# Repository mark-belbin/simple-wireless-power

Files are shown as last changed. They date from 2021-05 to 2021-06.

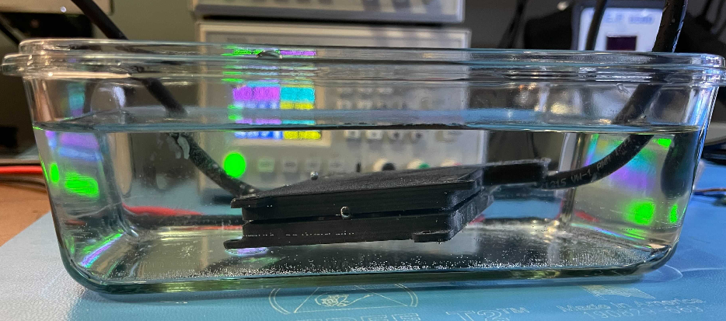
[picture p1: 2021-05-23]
docs/images/Water Setup.PNG

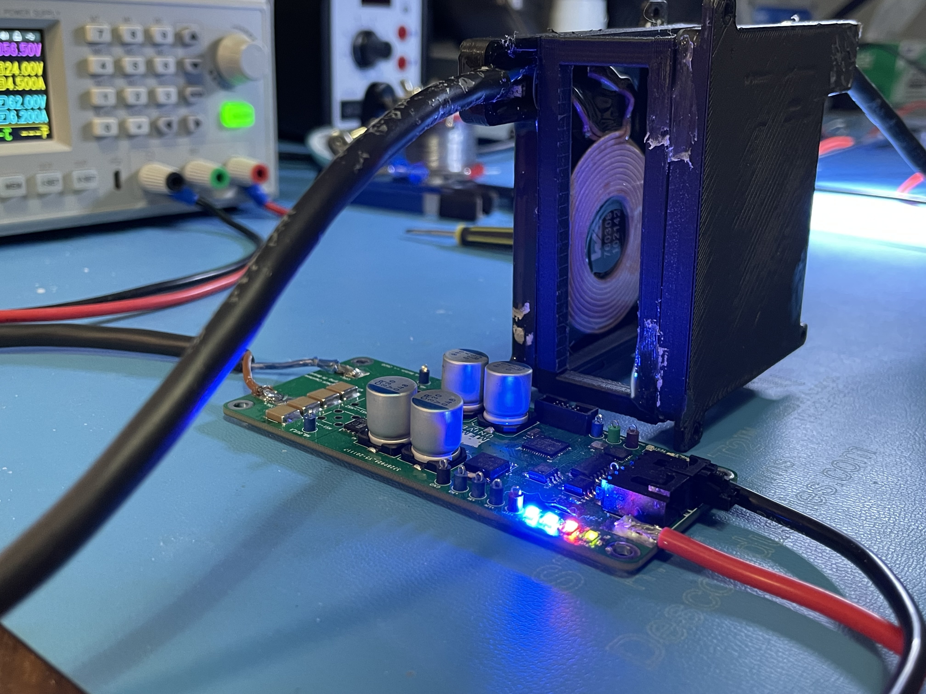
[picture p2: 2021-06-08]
docs/images/Gap Test.jpg

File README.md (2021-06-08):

# Simple Wireless Power System

## Introduction 
This project is a simple two-board wireless power system that can transmit up to 100W at close distances. Originally it was designed as a small part of a subsea resident autonomous underwater vehicle senior design project. The goal was to have a contactless method to charge the vehicles battery in an underwater docking station, versus a contact method like a wetmate connector. This reduces the chance for failure in a harsh ocean environment. Included in this repository are schematics, PCB design files, LTspice simulations, and embedded code.

TX Board Powered

## Design Topology
At the start of my wireless power investigation, it was initially decided to create a type of "coreless transformer" to keep things simple. This type of design would transfer power by simply placing two identical coils as close as possible to each other. The closer the coils, the higher their mutal inductance and coupling coefficient. The coupling coefficient directly equals the maximum achievable efficiency; k=0.7 would mean 70% efficiency for example. 

coreless_transformer
> Coreless transformer equivalent circuit.

However, since a lot of work was already being placed into research and simulation anyways, it was decided to try and create a resonant system. Using capactiors, resonant circuits can be created with the inductive transmitter and reciever coils, increasing efficiency accross the wireless link. This is the de facto inductive wireless power transfer method used in industry, and it turned out to be simpler than thought. The topology chosen is called "series-series" resonant inductive wireless power transfer, which means that the compensating capacitors are placed in series with both the transmit and recieve coils. Other topologys exist such as "series-parallel" or "parallel-parallel" which place the capacitors in parallel with the coils as well.

series_series
> Series-series topology circuit.

## Hardware
The system consists of a transmitter (TX) PCB and a reciever (RX) PCB. Both are 4 layer 1oz copper boards that are 100x45mm. The designs were completed using KiCAD EDA (http://kicad-pcb.org/), a free and open source PCB design software that is highly recommended. 

### TX Board
The transmitter board's primary purpose is to take a DC input voltage and pass it through a full bridge inverter to create a high frequency sinusoidal voltage. This sinusoidal voltage passes through the compensating capacitors and transmitter coil, and creates an alternating magnetic field that couples to the reciever coil. The H-Bridge is designed around an operating point of 24VDC input, 100kHz switching frequency, and up to 100W of transfer power. The main limiter for power transfer is the rated voltage and current of the coils and compensating capacitors. The MOSFETs of the H-Bridge are over-speced to minimize losses. Short circuit protection circuitry is included on the TX board, since if the TX coil is open-loaded during operation it will appear as a short to the input power supply.

TX Board

The TX board also has an embedded SAMD21 microntroller which generates the nessecary PWM signal for the gate drivers. Further, the board includes a CAN controller and transceiver so that it could potentially be commanded on/off and relay power transfer telemetry to a remote control computer via CANBus.

TX Schematic

### RX Board
The RX board is much simpler than the TX board. It has no microcontroller, and uses passive schottky diodes in a full bridge rectifier configuration to convert the recieved AC voltage back to a usable DC voltage. An simple overvoltage protection scheme is incorporated in the RX board to prevent an overvoltage event downstream. A schmitt trigger circuit watches the output voltage, and if it is too high, connects the output to a bank of bleeder resistors. The extra load on the output subsequently draws down the voltage before it reaches a harmful level. 
                                                                                   
RX Board

RX Schematic

### Key Components

#### Coils
The transmitter and reciever coils are identical. They were sourced on Digi-Key from Wurth Electronics, PN 732-9670-ND. They have an inductance of 5.8uH, and a very low series resistance, allowing for high current rating. I think these are probably the highest current rated coils you can find on Digikey when I selected them! As well, Wurth was kind enough to provide ample documentation for the coils. A key piece of data was a graph of their Quality factor (Q) versus frequency. The higher the quality factor, the better the efficiency. Therefore, since the Q peaked at around 100-101kHz, that was the selected operating frequency for the entire system.

Coils
> Coils encased and epoxyed in a custom mount for underwater use in the original AUV application. 

#### Series Capacitors
Four 100nF capacitors were placed in parallel to achieve the desired ~380-400nF series capacitance. Large 2220 package ceramic capacitors were chosen for their desirable low series resistance. The final parts were chosen from Murata Electronics and sourced on Digikey, PN 490-16696-1-ND. These capacitors were compared against others, again looking at their quality factor over frequency. The series capacitors ended up being the weakest link in the system, and would fail on the TX side when delivering over 5-6A. These caps had the best that could be found at the time, but if someone knows of a better or higher current-carrying choice, let me know! 

#### MOSFETs
The MOSFETs chosen are low-loss N-Channel devices. The final parts chosen are from Infineon and sourced on Digi-Key, PN 448-IAUC70N08S5N074ATMA1CT-ND. These FETs were selected for the lowest possible loss, taking into account both resistive and switching losses. 

#### Diodes
The diodes for the full-bridge rectifier were chosen again for as low of loss as possible. Really, the low voltage and high current environment is probably better suited for active rectification, but to keep things simple passive rectification was chosen. The best diodes for this are schottky due to their low forward voltage. The final parts chosen are from ON Semi and sourced from Digi-Key, PN FSV12100VCT-ND. A few different diode models were selected and simulated in the final circuit, and this model ended up producing the lowest loss. 

#### Micro Controller
The chosen microcontroller is the SAMD21G18A, PN ATSAMD21G18A-MF-ND. This is the same microcontroller that is on the Arduino Zero dev board, and our senior design team already knew how to easily program and flash it. Perhaps someone could modify this design and retrofit a more popular microcontroller, like an STM32.

## Software
The current software developed for this project is the embedded code on the TX board's SAMD21 microcontroller. Code was developed using the Arduino IDE for simplicity. A .bin file was generated and then uploaded to the microcontroller using a J-Link EDU programmer. The code is about as simple as it gets, just generating a 50% duty cycle, 100kHz PWM signal. No feedback is incorporated since it is assumed that there is no expected communication between TX and RX boards in the original underwater application. 

## Simulation
The entire end-to-end wireless power system was simulated in LTspice. The simulation aided in component selection, and gave an initial estimate of efficiency greater than 90%. It's hard to say how accurate the simulation is, since it's not clear what coupling factor, k, will be present in a real world system. Any tips on WPT system simulation in LTspice would be greatly appreciated! 

Sim Schematic

## Testing Results
The system was tested with surpising results. At a gap distance of about 1-2mm, as close as we could get, the system was able to transfer power up to 100W at an efficiency of 81.3%. Testing different frequencies between 95-105kHz did not show any noticeable difference in efficiency. The coils were also submerged in saltwater to check efficiency versus the in-air test. There was no measurable difference in water, salt or fresh.

Lab Test Setup

Water Setup

Another interesting outcome was shown in the thermal images during testing. The hottest components in the system were the series capacitors, reaching upwards of 70C degrees after 5 mins of operation. No heatsink or airflow meant that these are probably worst case numbers, but still perhaps the capacitors could be underspec'd for the application. At 100W delivered, about 20W is lost in the system, and the series capacitors are the only noticeable components that heat up significantly. It's a bit inconcievable that all the 20W is split amongst 8 small capacitors, so I assume that there are some losses in the surrounding air that are radiated away. It's hard to tell, would definitely be open to some insight on this if anyone has encountered this before! 

capacitor_thermals

Efficiency vs coil gap distance measurements were completed with some interesting results. First, efficiency seems to drop linearly from 0-20mm. This is cool since it seems that the resonant effect is indeed working. Normally a magnetic field would decrease with the distance squared, a non-linear relationship. As well, when reaching 20mm or beyond, the TX board was limited by its series current capability. More series current is required in to the transmitter coil to achieve the same power transfer as efficiency drops. The series capacitors on the TX board were the limiter, as they started to fail beyond 6A. A heatsink and forced air could give them a bit of extra capability potentially. I'd be interested in hearing about any better capacitor choices for higher series current while maintaining low loss accross them, or perhaps if a parallel-series or parallel-parallel topology would solve this problem.

Gap Test

GapGraph

## Discussion
This was a fun project and a small part of a much larger senior design project. 80-75% efficiency for 0-5mm coil gap satisfies the original design problem, which was to safely deliver 50W underwater at a 0-5mm gap distance. Always open for discussion or any tips on how this could have been done better. For a future project I'm interested in trying to make a super small low power version that could deliver 5-10W for underwater sensor applications.

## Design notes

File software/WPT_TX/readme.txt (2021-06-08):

Software:
Programming Notes
Install arduino zero boards
Arduino IDE, Export Binary,
program bin with segger j flash and jlink edu
But in boards.txt edit with to 'without' under arduino zero board

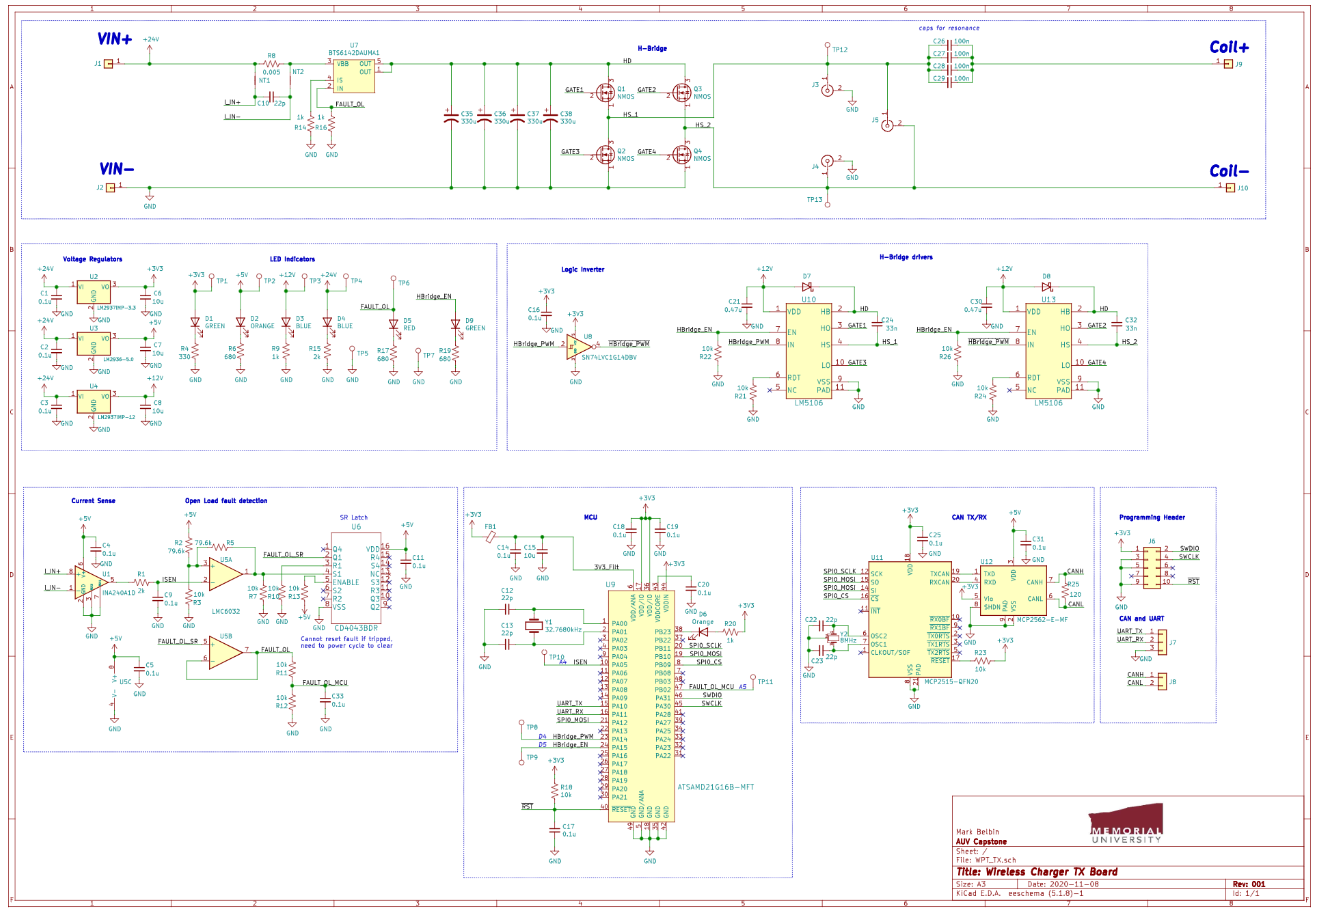
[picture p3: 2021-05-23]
docs/images/TX Schematic.PNG

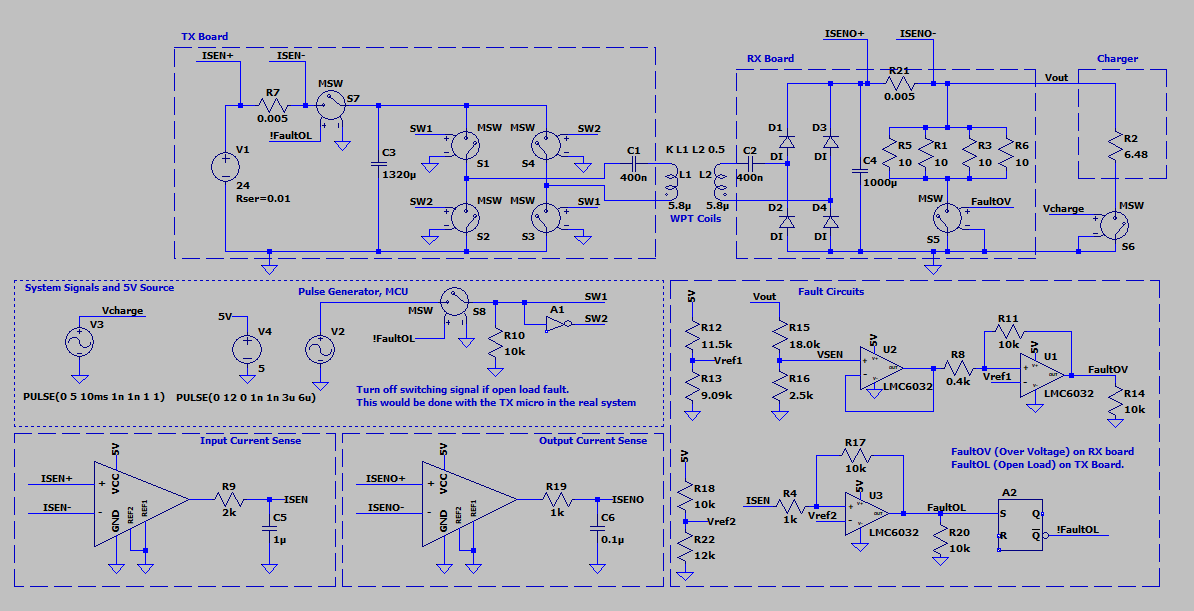
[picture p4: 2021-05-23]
docs/images/Sim Schematic.PNG

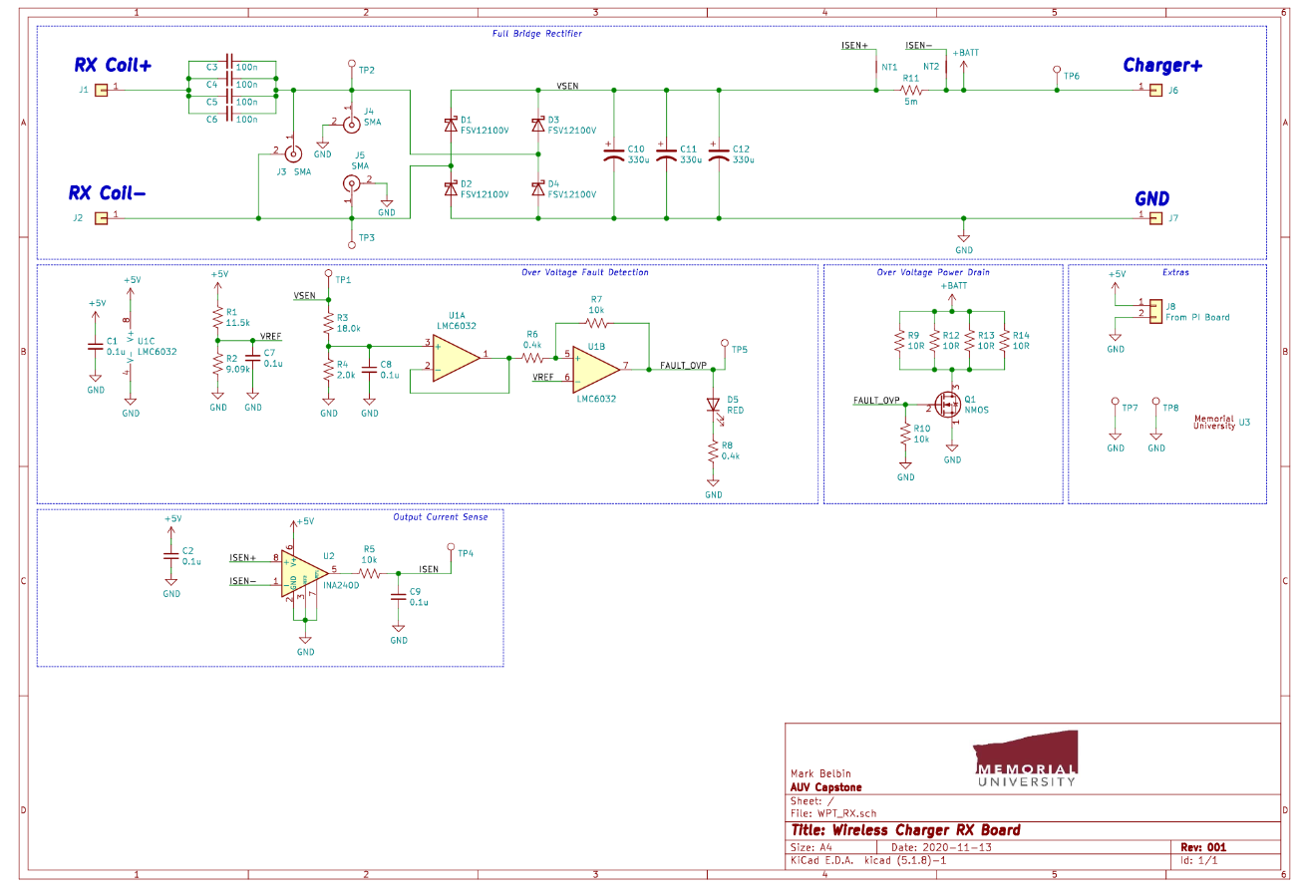
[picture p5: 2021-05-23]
docs/images/RX Schematic.PNG

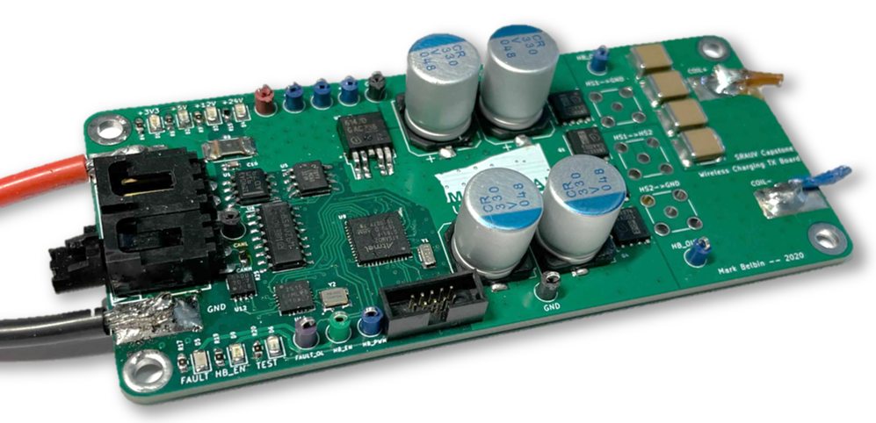
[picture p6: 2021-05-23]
docs/images/TX Board.PNG

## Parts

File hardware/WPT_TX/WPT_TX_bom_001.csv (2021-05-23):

Component | Description | Part | References | Value | Footprint | Quantity Per PCB | Datasheet | Digikey
1 | Unpolarized capacitor, small symbol | C_Small | C1 C2 C3 C4 C5 C9 C11 C14 C16 C17 C18 C19 C20 C25 C31 C33 | 0.1u | C_0603_1608Metric | 16 | ~ | 1276-1941-1-ND 1276-1258-1-ND
2 | Unpolarized capacitor, small symbol | C_Small | C21 C30 | 0.47u | C_0805 | 2 | ~ | 478-10438-1-ND
3 | Unpolarized capacitor, small symbol | C_Small | C26 C27 C28 C29 | 100n | C_2220 | 4 | ~ | 490-16696-1-ND
4 | Unpolarized capacitor, small symbol | C_Small | C15 | 10u | C_0603_1608Metric | 1 | ~ | 490-7201-1-ND
5 | Unpolarized capacitor, small symbol | C_Small | C6 C7 C8 | 10u | C_1206 | 3 | ~ | 1276-6767-1-ND
6 | Unpolarized capacitor, small symbol | C_Small | C10 C12 C13 C22 C23 | 22p | C_0603_1608Metric | 5 | ~ | 720-VJ0603A220JXBACCT-ND
7 | Unpolarized capacitor, small symbol | C_Small | C24 C32 | 33n | C_0805 | 2 | ~ | 445-172691-1-ND
8 | Light emitting diode | LED | D3 D4 | BLUE | LED_0805_2012Metric | 2 | ~ | 160-1579-1-ND
9 | Schottky diode | D_Schottky | D7 D8 | D_Schottky | D_SMA | 2 | ~ | SS16T3GOSCT-ND
10 | Light emitting diode | LED | D1 D9 | GREEN | LED_0805_2012Metric | 2 | ~ | 160-1423-1-ND
11 | Light emitting diode | LED | D2 D6 | ORANGE | LED_0805_2012Metric | 2 | ~ | 160-1413-1-ND
12 | Light emitting diode | LED | D5 | RED | LED_0805_2012Metric | 1 | ~ | 475-1415-1-ND
13 | Ferrite bead, small symbol | Ferrite_Bead_Small | FB1 | FB | L_0805_2012Metric | 1 | ~ | 490-9706-1-ND
14 | Generic connector, single row, 01x01, script generated (kicad-library-utils/schlib/autogen/connector/) | Conn_01x01 | J1 J2 J9 J10 | Conn_01x01 | SolderWirePad_single_SMD_5x10mm | 4 | ~
15 | Generic connector, single row, 01x03, script generated (kicad-library-utils/schlib/autogen/connector/) | Conn_01x03 | J7 | Conn_01x03 | 70553-03 | 1 | ~ | WM4154-ND
16 | Generic connector, single row, 01x02, script generated (kicad-library-utils/schlib/autogen/connector/) | Conn_01x02 | J8 | Conn_01x04 | 70553-02 | 1 | ~ | WM4900-ND
17 | Generic connector, double row, 02x05, odd/even pin numbering scheme (row 1 odd numbers, row 2 even numbers), script generated (kicad-library-utils/schlib/autogen/connector/) | Conn_02x05_Odd_Even | J6 | Conn_02x05_Odd_Even | Pin_Header_Straight_2x05_Pitch1.27mm | 1 | ~ | 1175-1627-ND
18 | coaxial connector (BNC, SMA, SMB, SMC, Cinch/RCA, ...) | Conn_Coaxial | J3 J4 J5 | Conn_Coaxial | SMA_Amphenol_901-144_Vertical | 3 | ~ | WM17068-ND
19 | Net tie, 2 pins | Net-Tie_2 | NT1 NT2 | Net-Tie_2 | NetTie-2_SMD_Pad0.25mm | 2 | ~
20 | N-MOSFET transistor, source/gate/drain | Q_NMOS_SGD | Q1 Q2 Q3 Q4 | NMOS | TDSON-8-1 | 4 | https://www.infineon.com/dgdl/Infineon-IAUC70N08S5N074-DS-v01_00-EN.pdf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 | 448-IAUC70N08S5N074ATMA1CT-ND
21 | Resistor, US symbol | R_US | R8 | 0.005 | R_2512_Sense | 1 | ~ | YAG6124CT-ND
22 | Resistor, US symbol | R_US | R3 R7 R10 R11 R12 R13 R18 R21 R22 R23 R24 R26 | 10k | R_0603_1608Metric | 12 | ~ | RHM10KDCT-ND
23 | Resistor, US symbol | R_US | R25 | 120 | R_0603_1608Metric | 1 | ~ | P120BYTR-ND
24 | Resistor, US symbol | R_US | R9 R14 R16 R20 | 1k | R_0603_1608Metric | 4 | ~ | RHM1.0KDCT-ND
25 | Resistor, US symbol | R_US | R1 R15 | 2k | R_0603_1608Metric | 2 | ~ | 541-2790-1-ND
26 | Resistor, US symbol | R_US | R4 | 330 | R_0603_1608Metric | 1 | ~ | RHM330DCT-ND
27 | Resistor, US symbol | R_US | R6 R17 R19 | 680 | R_0603_1608Metric | 3 | ~ | RHM680DCT-ND
28 | Resistor, US symbol | R_US | R2 R5 | 79.6k | R_0603_1608Metric | 2 | ~ | 13-RT0603BRD0779K6LCT-ND
29 | IC MCU 32BIT 64KB FLASH 48QFN | ATSAMD21G16B-MFT | U9 | ATSAMD21G16B-MFT | TQFP-48_7x7mm | 1 | http://www.microchip.com/mymicrochip/filehandler.aspx?ddocname=en590209 | ATSAMD21G18A-MF-ND
30 |  | BTS6142DAUMA1 | U7 | BTS6142DAUMA1 | TO-252-4 | 1 | https://www.infineon.com/dgdl/Infineon-BTS6142D-DS-v01_01-EN.pdf?fileId=5546d4625a888733015aa3da1e0e1026 | BTS6142DAUMA1CT-ND
31 |  | CD4043BDR | U6 | CD4043BDR | SOIC-16_3.9x9.9mm_Pitch1.27mm | 1 |  | 296-31496-1-ND
32 | High- and Low-Side, Bidirectional, Zero-Drift, Current-Sense Amplifier With Enhanced PWM Rejection, 20V/V, SOIC-8 | INA240A1D | U1 | INA240A1D | SOIC-8_3.9x4.9mm_P1.27mm | 1 | http://www.ti.com/lit/ds/symlink/ina240.pdf | 296-48837-ND
33 | 50mA Ultra-Low Quiescent Current LDO Voltage Regulator, 5.0V fixed output, TO-252/SOT-223 | LM2936-5.0 | U3 | LM2936-5.0 | SOT-223-3_TabPin2 | 1 | http://www.ti.com/lit/ds/symlink/lm2936.pdf | 296-37374-1-ND
34 | 500-mA Low Dropout Regulator, SOT-223 | LM2937xMP | U4 | LM2937IMP-12 | SOT-223-3_TabPin2 | 1 | http://www.ti.com/lit/ds/symlink/lm2937.pdf | LM2937IMP-12/NOPBCT-ND
35 | 500-mA Low Dropout Regulator, SOT-223 | LM2937xMP | U2 | LM2937IMP-3.3 | SOT-223-3_TabPin2 | 1 | http://www.ti.com/lit/ds/symlink/lm2937.pdf | LM2937IMPX-3.3/NOPBCT-ND
36 |  | LM5106SD_NOPB | U10 U13 | LM5106 | LM5106SD | 2 |  | LM5106SD/NOPBCT-ND
37 | Precision CMOS Dual Operational Amplifier, DIP-8/SOIC-8 | LMC6082 | U5 | LMC6032 | SOIC-8_3.9x4.9mm_Pitch1.27mm | 1 | http://www.ti.com/lit/ds/symlink/lmc6082.pdf | 296-49646-1-ND
38 |  | MCP2515-QFN20 | U11 | MCP2515-QFN20 | TSSOP-20_4.4x6.5mm_P0.65mm | 1 |  | MCP2515-E/ML-ND
39 | High-Speed CAN Transceiver, 1Mbps, 5V supply, Vio pin, -40C to +125C, DFN-8 | MCP2562-E-MF | U12 | MCP2562-E-MF | DFN-8-1EP_3x3mm_P0.65mm_EP1.55x2.4mm | 1 | http://ww1.microchip.com/downloads/en/DeviceDoc/25167A.pdf | MCP2562-E/MF-ND
40 | Single Schmitt-Trigger Inverter, SOT-23 | SN74LVC1G14DBV | U8 | SN74LVC1G14DBV | SOT-23-5 | 1 | http://www.ti.com/lit/ds/symlink/sn74lvc1g14.pdf | 296-35944-1-ND
41 | Two pin crystal | Crystal | Y1 | 32.7680kHz | Crystal_SMD_3215-2pin_3.2x1.5mm | 1 | ~ | 887-2605-1-ND
42 | Three pin crystal, GND on pin 2, small symbol | Crystal_GND2_Small | Y2 | 8MHz | OSCCC320X250 | 1 | ~ | 2151-RH100-8.000-20-3050-EXT-TRCT-ND
Component Groups: | 42
Component Count: | 100
Fitted Components: | 100
Number of PCBs: | 1
Total components: | 100
Schematic Version: | 001
Schematic Date: | 2020-11-08
PCB Variant: | [u'default']
BoM Date: | 2020-11-08 10:35:57 PM
Schematic Source: | D:\AUV Capstone\AUV-Senior-Design\Mark\WPT_TX\WPT_TX.sch
KiCad Version: | Eeschema (5.1.8)-1

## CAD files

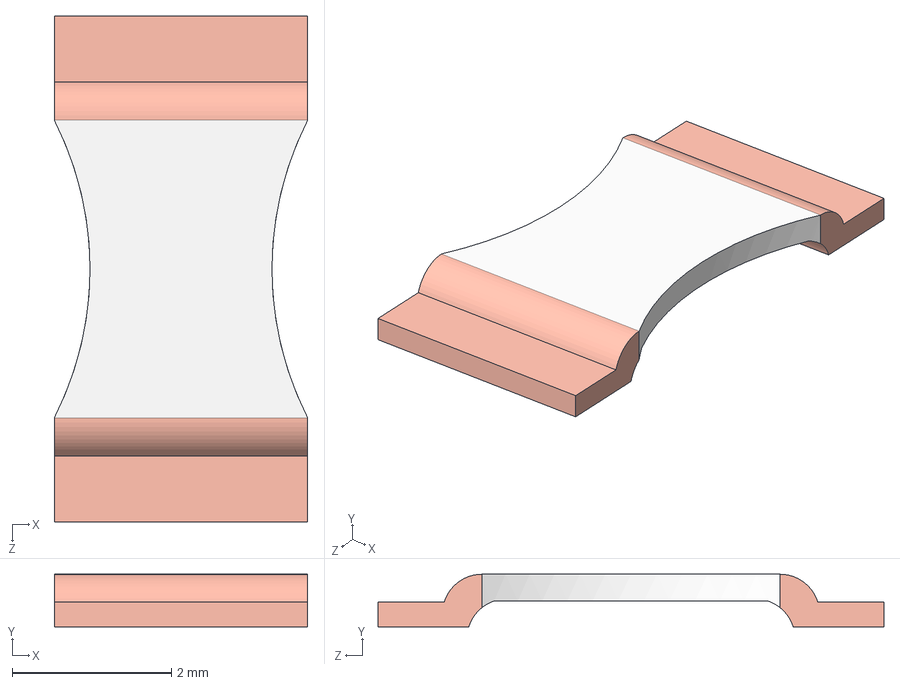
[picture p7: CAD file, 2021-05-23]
hardware/WPT_RX/3D Models/Sense Resistor.STEP
3.18 x 0.66 x 6.35 mm

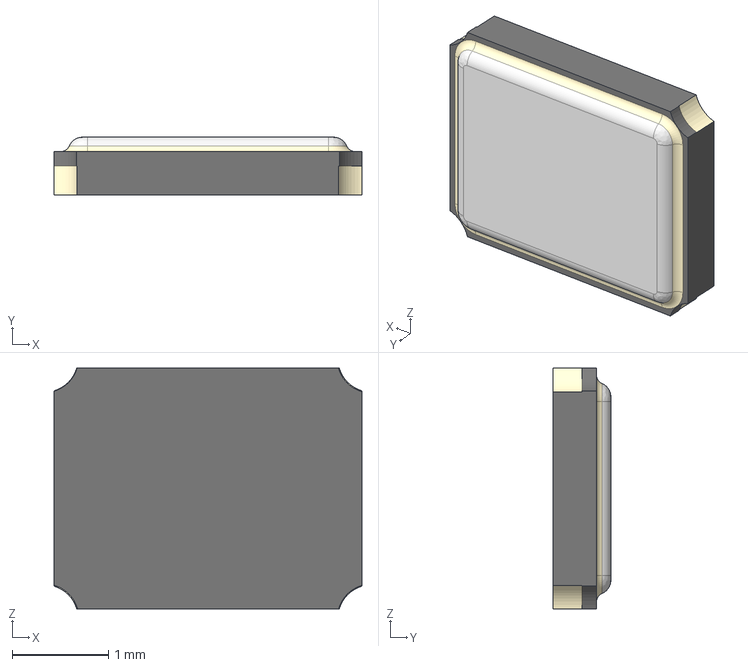
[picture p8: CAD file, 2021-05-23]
hardware/WPT_RX/3D Models/KX7 SMD Quartz Crystal Resonator 3.2x2.5mm.step
3.20 x 0.6 x 2.50 mm

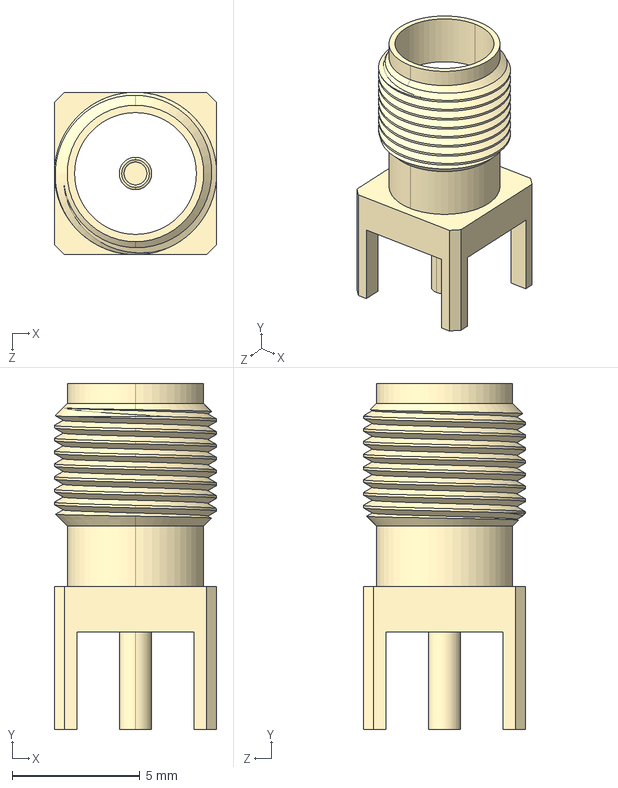
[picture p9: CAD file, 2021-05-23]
hardware/WPT_RX/3D Models/SMA Vertical.step
6.35 x 13.5 x 6.35 mm

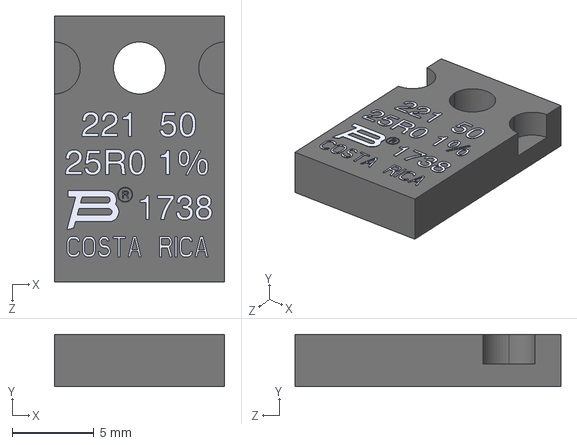
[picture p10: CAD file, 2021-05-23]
hardware/WPT_RX/3D Models/PWR221T-50.STEP
10.4 x 3.20 x 16.3 mm

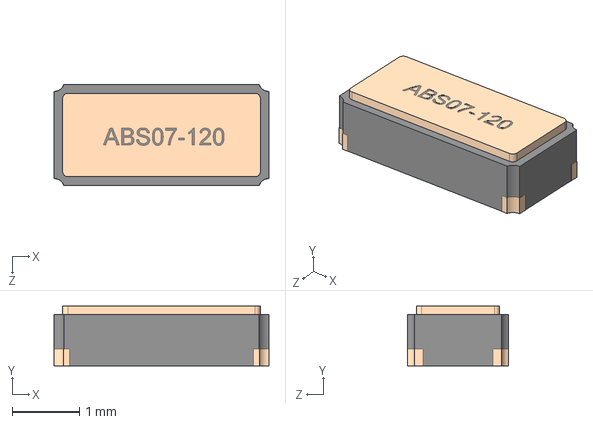
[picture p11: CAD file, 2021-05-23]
hardware/WPT_TX/3D Models/ABS07-120.STEP
3.21 x 0.889 x 1.50 mm

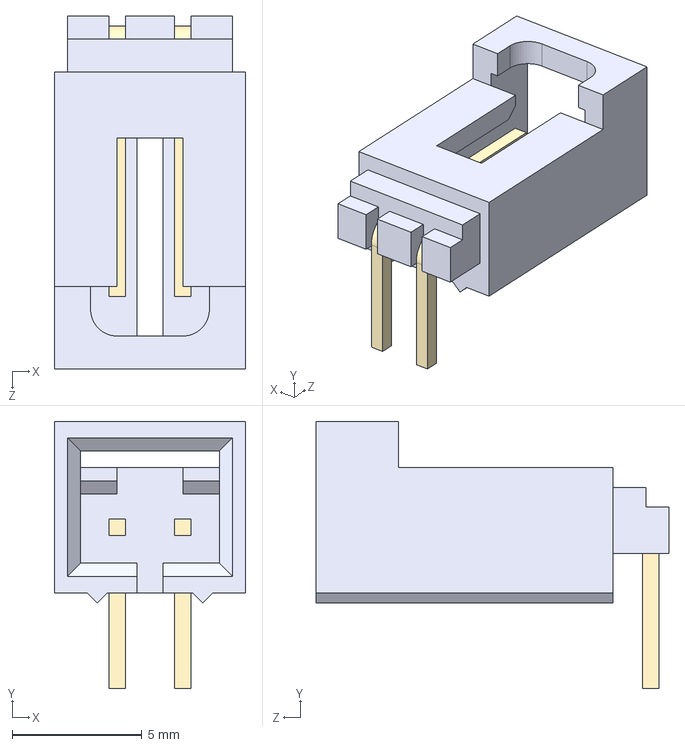
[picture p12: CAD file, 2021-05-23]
hardware/WPT_TX/3D Models/705530001.STEP
7.37 x 10.3 x 13.6 mm

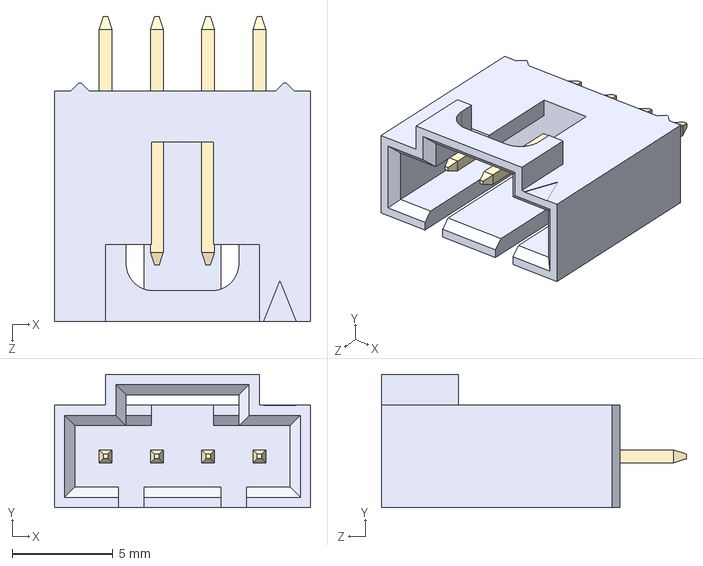
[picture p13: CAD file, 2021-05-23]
hardware/WPT_TX/3D Models/705430003.STEP
12.7 x 6.60 x 15.1 mm

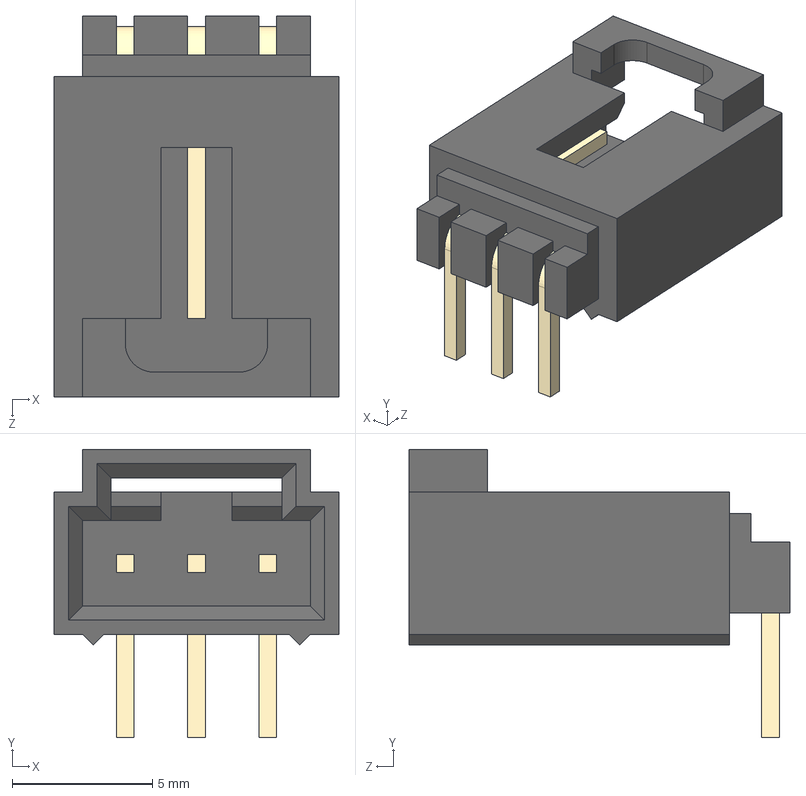
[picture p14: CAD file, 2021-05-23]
hardware/WPT_TX/3D Models/705530002.STEP
10.2 x 10.3 x 13.6 mm

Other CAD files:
hardware/WPT_RX/3D Models/PWR221T-50.SLDPRT
hardware/WPT_RX/3D Models/PWR221T-50.stp

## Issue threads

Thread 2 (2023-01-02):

Issue sharing

briansune, 2023-01-02:
@mark-belbin

I would like to know why selecting a X7R capacitor?
X7R will decrease capacitance along the voltage bias.
C0G or NPO would be a better selection.

Meanwhile, if the voltage is biased at 50VAC then the drop is about 10% each parallel capacitor you had connected.
This means the effective switch frequency no long 400nF but around 360nF or less.

Please share a bit more the HW you had experience and make things better.

Thank you

Closed 2023-01-11.

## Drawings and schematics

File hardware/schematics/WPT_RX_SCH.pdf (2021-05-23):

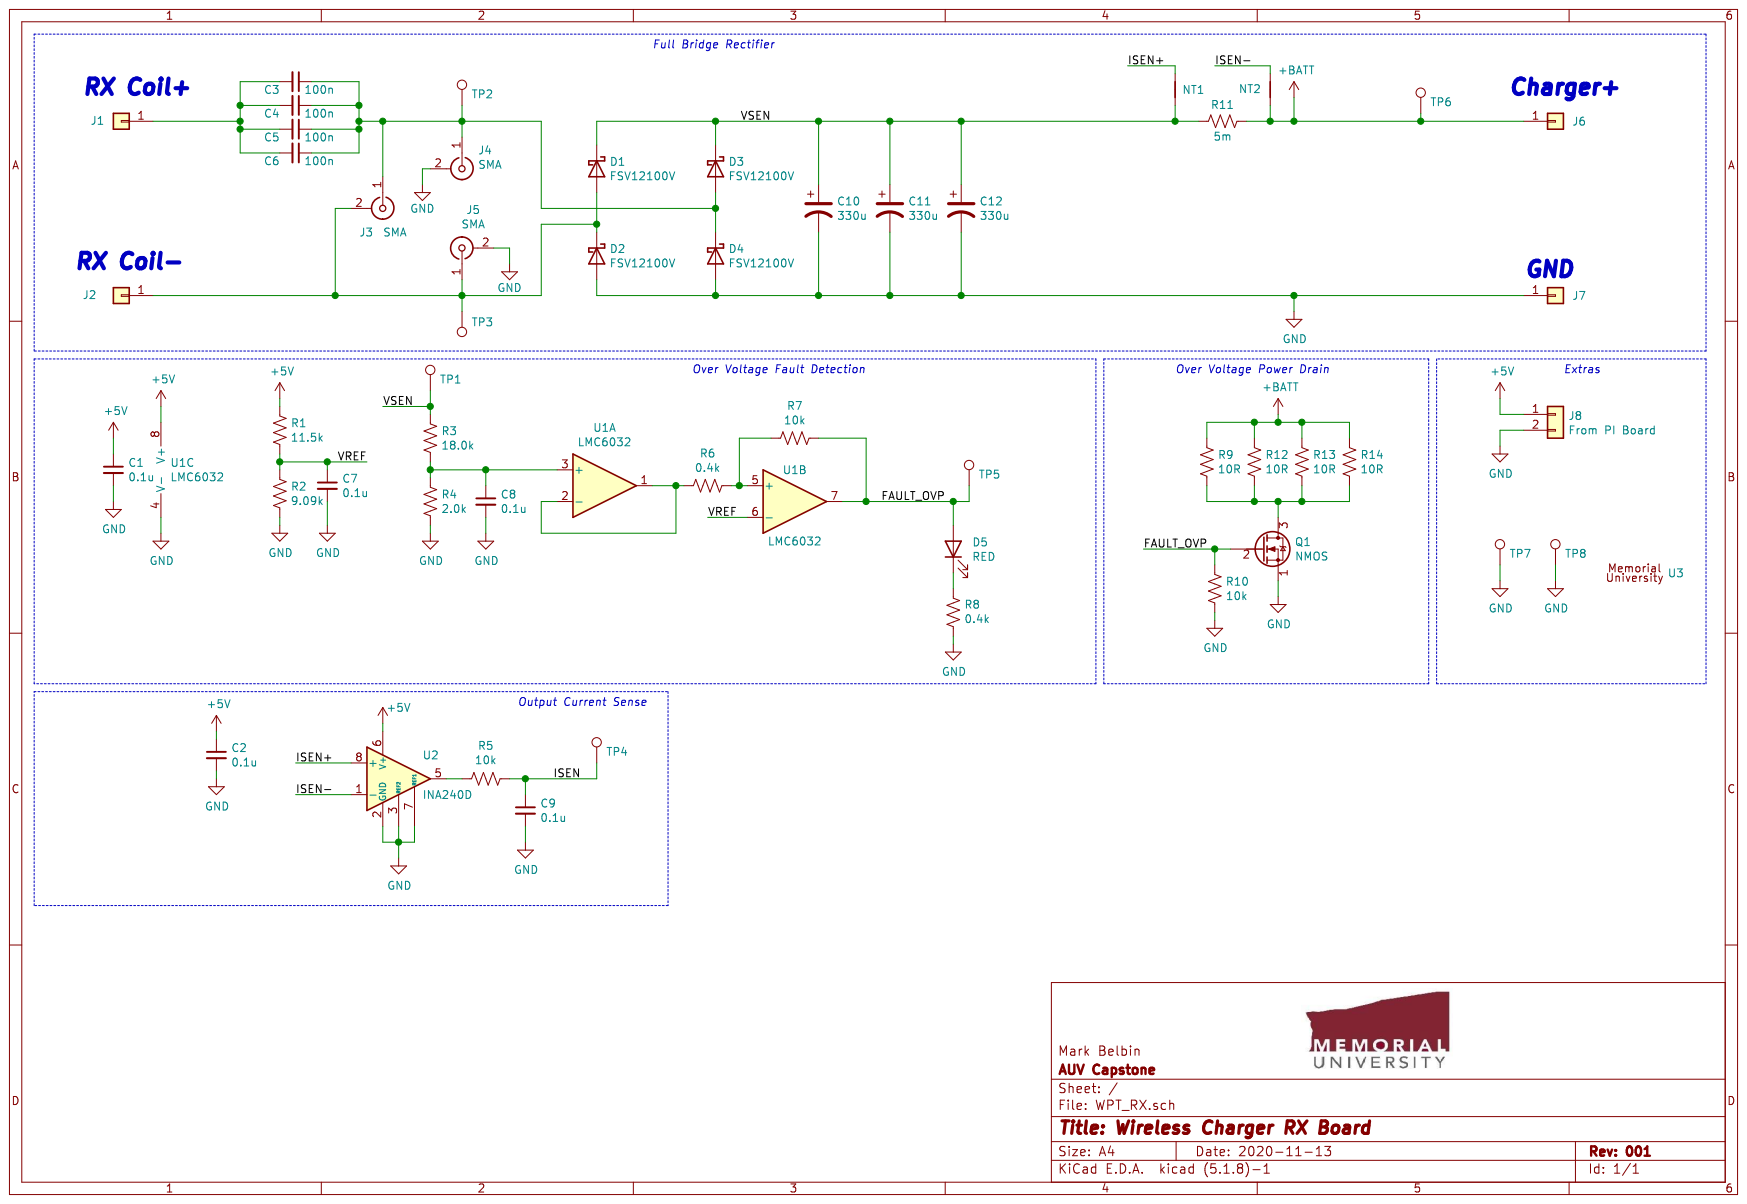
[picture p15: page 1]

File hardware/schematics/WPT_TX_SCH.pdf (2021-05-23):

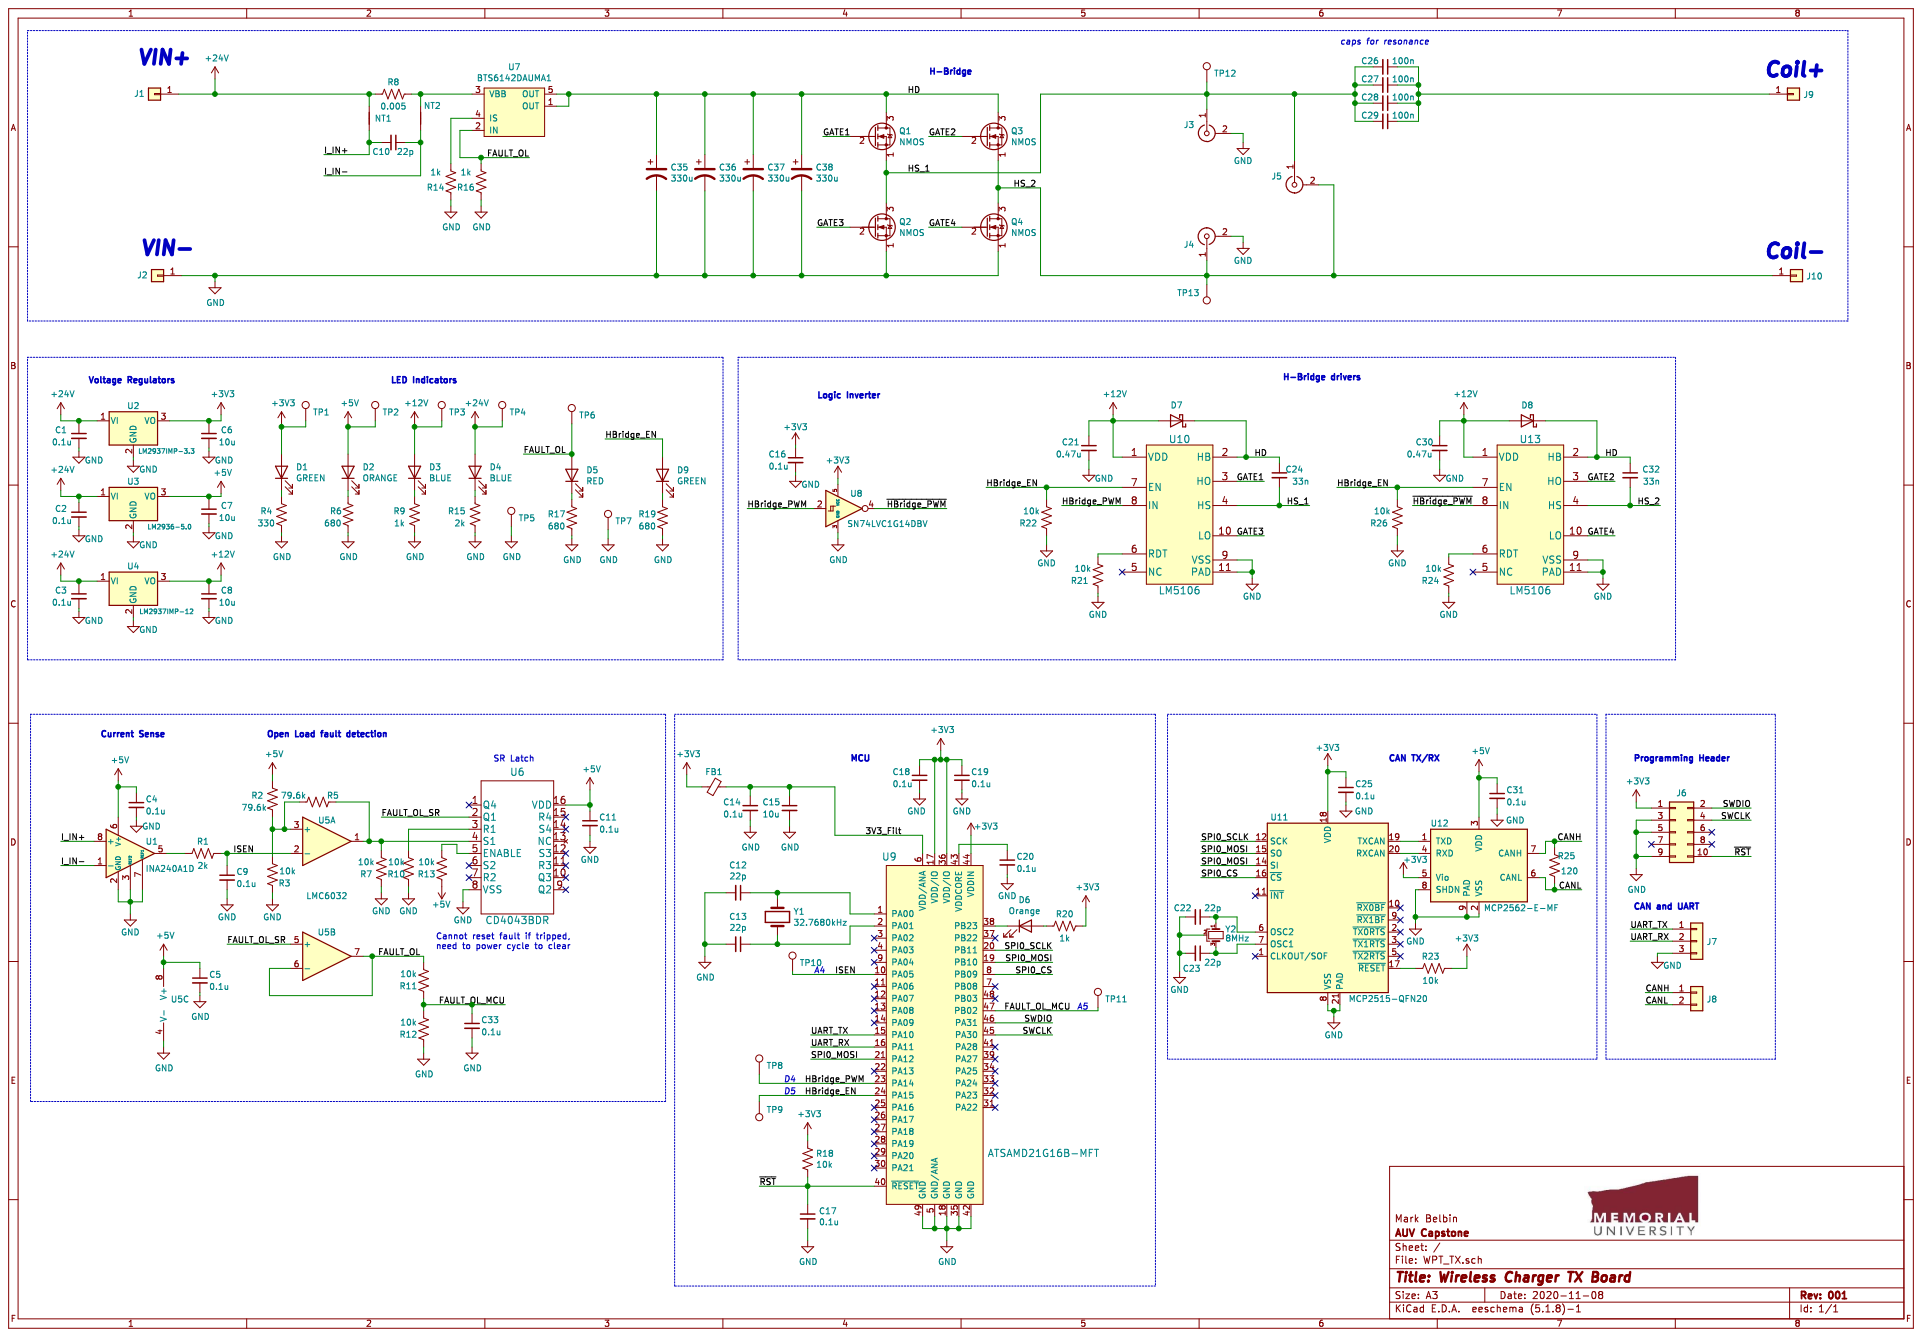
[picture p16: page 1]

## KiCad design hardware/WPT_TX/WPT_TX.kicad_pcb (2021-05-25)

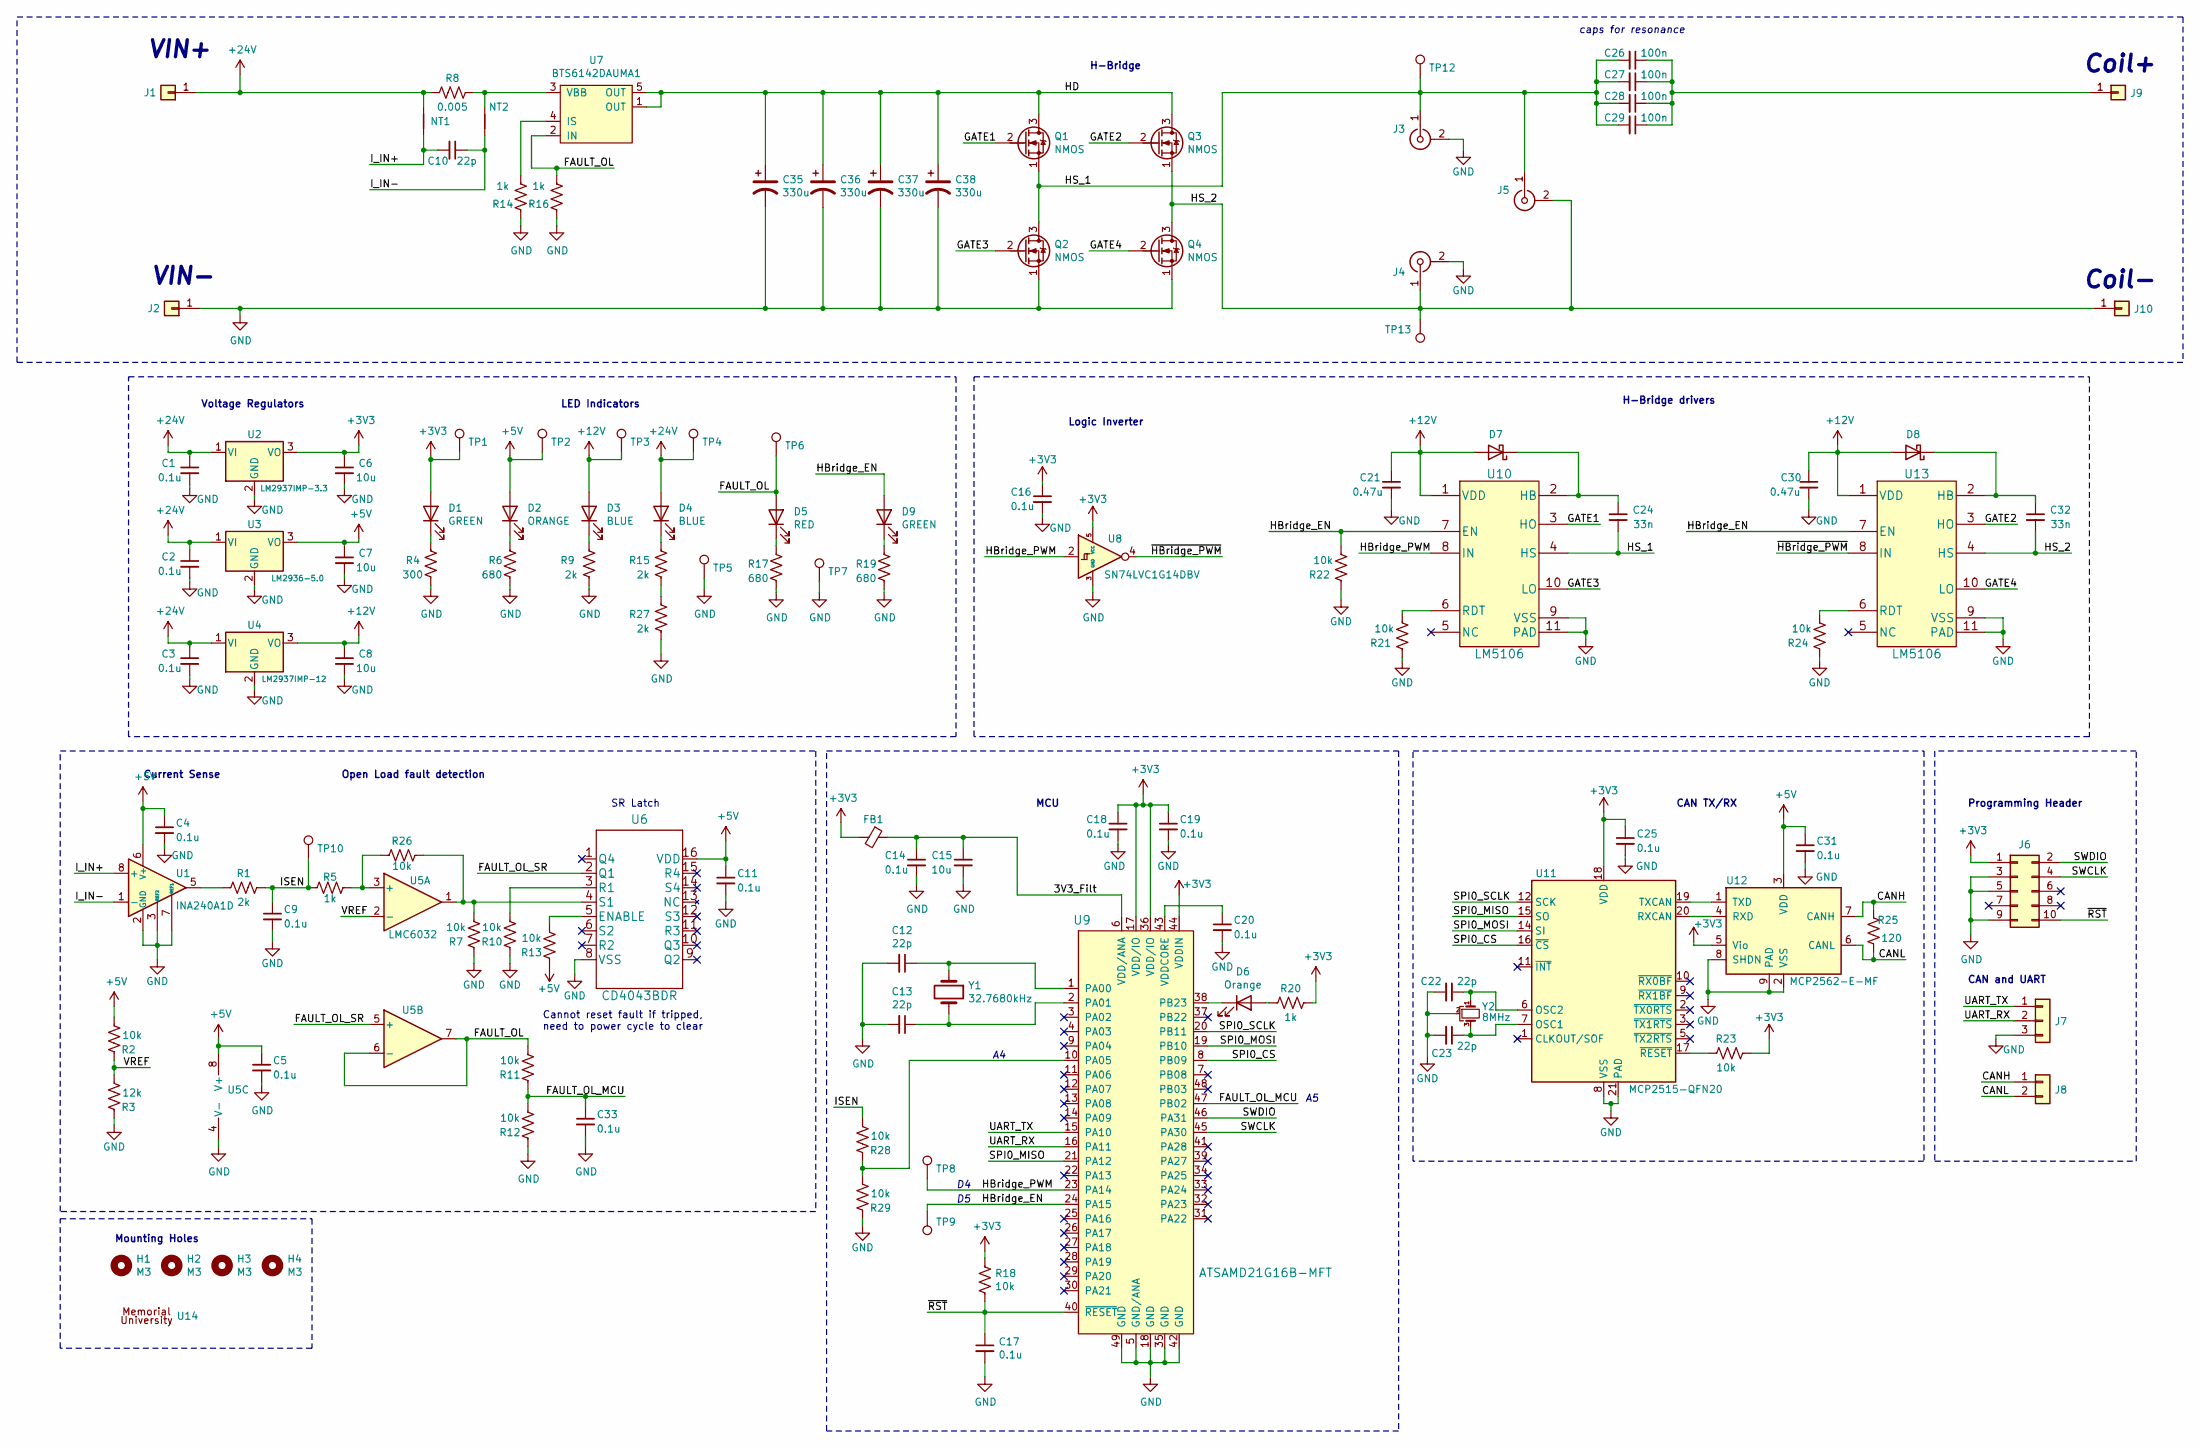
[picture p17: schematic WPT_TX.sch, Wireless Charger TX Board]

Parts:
C1, C2, C3: 0.1u; C_0603_1608Metric; Digikey 1276-1941-1-ND
C4, C5, C9, C11, C14, C16, C17, C18, C19, C20, C25, C31, C33: 0.1u; C_0603_1608Metric; Digikey 1276-1258-1-ND
C6, C7, C8: 10u; C_1206_3216Metric; Digikey 1276-6767-1-ND
C10, C12, C13, C22, C23: 22p; C_0603_1608Metric; Digikey 720-VJ0603A220JXBACCT-ND
C15: 10u; C_0603_1608Metric; Digikey 490-7201-1-ND
C21, C30: 0.47u; C_0805_2012Metric; Digikey 478-10438-1-ND
C24, C32: 33n; C_0805_2012Metric; Digikey 445-172691-1-ND
C26, C27, C28, C29: 100n; C_2220_5650Metric; Digikey 490-16696-1-ND
C35, C36, C37, C38: 330u; CP_Elec_10x12.5; Digikey 493-13765-1-ND
D1, D9: GREEN; LED_0805_2012Metric; Digikey 160-1423-1-ND
D2: ORANGE; LED_0805_2012Metric; Digikey 160-1413-1-ND
D3, D4: BLUE; LED_0805_2012Metric; Digikey 160-1579-1-ND
D5: RED; LED_0805_2012Metric; Digikey 475-1415-1-ND
D6: Orange; LED_0805_2012Metric; Digikey 160-1413-1-ND
D7, D8: D_Schottky; D_SOD-323_HandSoldering; Digikey 641-1786-1-ND
FB1: FB; L_0805_2012Metric; Digikey 490-9706-1-ND
H1, H2, H3, H4: M3; MountingHole_3.2mm_M3_DIN965_Pad
J1, J2, J9, J10: Conn_01x01; SolderWirePad_single_SMD_5x10mm
J3, J4, J5: Conn_Coaxial; SMA_Amphenol_901-144_Vertical; Digikey WM17068-ND
J6: Conn_02x05_Odd_Even; PinHeader_2x05_P1.27mm_Vertical; Digikey 1175-1627-ND
J7: Conn_01x03; 70553-03; Digikey WM4154-ND
J8: Conn_01x04; 70553-02; Digikey WM4900-ND
NT1, NT2: Net-Tie_2; NetTie-2_SMD_Pad0.25mm
Q1, Q2, Q3, Q4: NMOS; TDSON-8-1; Digikey 448-IAUC70N08S5N074ATMA1CT-ND
R1, R9, R15, R27: 2k; R_0603_1608Metric; Digikey 541-2790-1-ND
R2, R7, R10, R11, R12, R13, R18, R21, R22, R23, R24, R26, R28, R29: 10k; R_0603_1608Metric; Digikey RHM10KDCT-ND
R3: 12k; R_0603_1608Metric; Digikey P12KDBCT-ND
R4: 300; R_0603_1608Metric; Digikey P300BZCT-ND
R5, R14, R16, R20: 1k; R_0603_1608Metric; Digikey RHM1.0KDCT-ND
R6, R17, R19: 680; R_0603_1608Metric; Digikey RHM680DCT-ND
R8: 0.005; R_2512_Sense; Digikey YAG6124CT-ND
R25: 120; R_0603_1608Metric; Digikey P120BYTR-ND
TP1, TP2, TP3, TP4: TestPoint; TestPoint_Loop_D1.80mm_Drill1.0mm_Beaded; Digikey 36-5000-ND
TP5, TP6, TP7: TestPoint; TestPoint_Loop_D1.80mm_Drill1.0mm_Beaded; Digikey 36-5001-ND
TP8, TP9, TP10, TP12, TP13: TestPoint; TestPoint_Loop_D1.80mm_Drill1.0mm_Beaded; Digikey 36-5117-ND
U1: INA240A1D; SOIC-8_3.9x4.9mm_P1.27mm; Digikey 296-48837-ND
U2: LM2937IMP-3.3; SOT-223-3_TabPin2; Digikey LM2937IMPX-3.3/NOPBCT-ND
U3: LM2936-5.0; SOT-223-3_TabPin2; Digikey 296-37374-1-ND
U4: LM2937IMP-12; SOT-223-3_TabPin2; Digikey LM2937IMP-12/NOPBCT-ND
U5: LMC6032; SOIC-8_3.9x4.9mm_P1.27mm
U6: CD4043BDR; SOIC-16_3.9x9.9mm_P1.27mm; Digikey 296-31496-1-ND
U7: BTS6142DAUMA1; TO-252-4; Digikey BTS6142DAUMA1CT-ND
U8: SN74LVC1G14DBV; TSOT-23-5; Digikey 296-35944-1-ND
U9: ATSAMD21G16B-MFT; QFN-48-1EP_7x7mm_P0.5mm_EP5.6x5.6mm; Digikey ATSAMD21G18A-MF-ND
U10, U13: LM5106; LM5106SD; Digikey LM5106SD/NOPBCT-ND
U11: MCP2515-QFN20; QFN-20-1EP_4x4mm_P0.5mm_EP2.5x2.5mm_ThermalVias; Digikey MCP2515-E/ML-ND
U12: MCP2562-E-MF; DFN-8-1EP_3x3mm_P0.65mm_EP1.55x2.4mm; Digikey MCP2562-E/MF-ND
U14: Munlogo; MUNLOGO
Y1: 32.7680kHz; Crystal_SMD_3215-2pin_3.2x1.5mm; Digikey ‎XC1656CT-ND‎
Y2: 8MHz; OSCCC320X250; Digikey 2151-RH100-8.000-20-3050-EXT-TRCT-ND

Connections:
+3V3: C6.1, C16.1, C18.1, C19.1, C25.1, D1.2 (A), FB1.2, J6.1, R18.1, R20.1, R23.1, TP1.1, U2.3 (VO), U8.5 (VCC), U9.17 (VDD/IO), U9.36 (VDD/IO), U9.44 (VDDIN), U11.18 (VDD), U12.5 (Vio)
+5V: C4.1, C5.1, C7.1, C11.1, C31.1, D2.2 (A), R2.2, R13.1, TP2.1, U1.6 (V+), U3.3 (VO), U5.8 (V+), U6.16 (VDD), U12.3 (VDD)
+12V: C8.1, C21.1, C30.1, D3.2 (A), D7.2 (A), D8.2 (A), TP3.1, U4.3 (VO), U10.1 (VDD), U13.1 (VDD)
+24V: C1.1, C2.1, C3.1, D4.2 (A), J1.1, NT1.1, R8.2, TP4.1, U2.1 (VI), U3.1 (VI), U4.1 (VI)
/3V3_Filt: C14.1, C15.1, FB1.1, U9.6 (VDD/ANA)
/CANH: J8.1, R25.2, U12.7 (CANH)
/CANL: J8.2, R25.1, U12.6 (CANL)
/FAULT_OL: D5.2 (A), R11.2, R16.2, TP6.1, U5.6 (-), U5.7, U7.2 (IN)
/FAULT_OL_MCU: C33.1, R11.1, R12.2, U9.47 (PB02)
/FAULT_OL_SR: U5.5 (+), U6.2 (Q1)
/GATE1: Q1.2 (G), U10.3 (HO)
/GATE2: Q3.2 (G), U13.3 (HO)
/GATE3: Q2.2 (G), U10.10 (LO)
/GATE4: Q4.2 (G), U13.10 (LO)
/HBridge_EN: D9.2 (A), R22.2, TP9.1, U9.24 (PA15), U10.7 (EN), U13.7 (EN)
/HBridge_PWM: TP8.1, U8.2, U9.23 (PA14), U10.8 (IN)
/HD: C35.1, C36.1, C37.1, C38.1, Q1.3 (D), Q3.3 (D), U7.1 (OUT), U7.5 (OUT)
/HS_1: C24.2, C26.2, C27.2, C28.2, C29.2, J3.1 (In), J5.1 (In), Q1.1 (S), Q2.3 (D), TP12.1, U10.4 (HS)
/HS_2: C32.2, J4.1 (In), J5.2 (Ext), J10.1, Q3.1 (S), Q4.3 (D), TP13.1, U13.4 (HS)
/ISEN: C9.1, R1.1, R5.2, R28.2, TP10.1
/I_IN+: C10.2, NT1.2, U1.8 (+)
/I_IN-: C10.1, NT2.1, U1.1 (-)
/SPI0_CS: U9.8 (PB09), U11.16 (~CS)
/SPI0_MISO: U9.21 (PA12), U11.15 (SO)
/SPI0_MOSI: U9.19 (PB10), U11.14 (SI)
/SPI0_SCLK: U9.20 (PB11), U11.12 (SCK)
/SWCLK: J6.4, U9.45 (PA30)
/SWDIO: J6.2, U9.46 (PA31)
/UART_RX: J7.2, U9.16 (PA11)
/UART_TX: J7.1, U9.15 (PA10)
/VREF: R2.1, R3.2, U5.2 (-)
/~HBridge_PWM~: U8.4, U13.8 (IN)
/~RST~: C17.1, J6.10, R18.2, U9.40 (~RESET)
GND: C1.2, C2.2, C3.2, C4.2, C5.2, C6.2, C7.2, C8.2, C9.2, C11.2, C12.2, C13.2, C14.2, C15.2, C16.2, C17.2, C18.2, C19.2, C20.2, C21.2, C22.2, C23.2, C25.2, C30.2, C31.2, C33.2, C35.2, C36.2, C37.2, C38.2, J2.1, J3.2 (Ext), J4.2 (Ext), J6.3, J6.5, J6.9, J7.3, Q2.1 (S), Q4.1 (S), R3.1, R4.1, R6.1, R7.1, R9.1, R10.1, R12.1, R14.1, R16.1, R17.1, R19.1, R21.1, R22.1, R24.1, R27.1, R29.1, TP5.1, TP7.1, U1.2 (GND), U1.3 (REF2), U1.4 (GND), U1.7 (REF1), U2.2 (GND), U3.2 (GND), U4.2 (GND), U5.4 (V-), U6.8 (VSS), U8.3 (GND), U9.5 (GND/ANA), U9.18 (GND), U9.35 (GND), U9.42 (GND), U9.49 (GND), U10.9 (VSS), U10.11 (PAD), U11.8 (VSS), U11.21 (PAD), U12.2 (VSS), U12.8 (SHDN), U12.9 (PAD), U13.9 (VSS), U13.11 (PAD), Y2.2
unnamed: C12.1, U9.1 (PA00), Y1.1
unnamed: C13.1, U9.2 (PA01), Y1.2
unnamed: C20.1, U9.43 (VDDCORE)
unnamed: C22.1, U11.6 (OSC2), Y2.1
unnamed: C23.1, U11.7 (OSC1), Y2.3
unnamed: C24.1, D7.1 (K), U10.2 (HB)
unnamed: C26.1, C27.1, C28.1, C29.1, J9.1
unnamed: C32.1, D8.1 (K), U13.2 (HB)
unnamed: D1.1 (K), R4.2
unnamed: D2.1 (K), R6.2
unnamed: D3.1 (K), R9.2
unnamed: D4.1 (K), R15.2
unnamed: D5.1 (K), R17.2
unnamed: D6.1 (K), U9.38 (PB23)
unnamed: D6.2 (A), R20.2
unnamed: D9.1 (K), R19.2
unnamed: NT2.2, R8.1, U7.3 (VBB)
unnamed: R1.2, U1.5
unnamed: R10.2, U6.3 (R1)
unnamed: R13.2, U6.5 (ENABLE)
unnamed: R14.2, U7.4 (IS)
unnamed: R15.1, R27.2
unnamed: R21.2, U10.6 (RDT)
unnamed: R23.2, U11.17 (~RESET)
unnamed: R24.2, U13.6 (RDT)
unnamed: R7.2, R26.1, U5.1, U6.4 (S1)
unnamed: R5.1, R26.2, U5.3 (+)
unnamed: R28.1, R29.2, U9.10 (PA05)
unnamed: U11.19 (TXCAN), U12.1 (TXD)
unnamed: U11.20 (RXCAN), U12.4 (RXD)

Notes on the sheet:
Coil+
VIN+
VIN-
Coil-
caps for resonance
Current Sense
Open Load fault detection
Voltage Regulators
MCU
CAN TX/RX
H-Bridge
H-Bridge drivers
Cannot reset fault if tripped, need to power cycle to clear
SR Latch
Logic Inverter
Programming Header
CAN and UART
LED Indicators
Mounting Holes

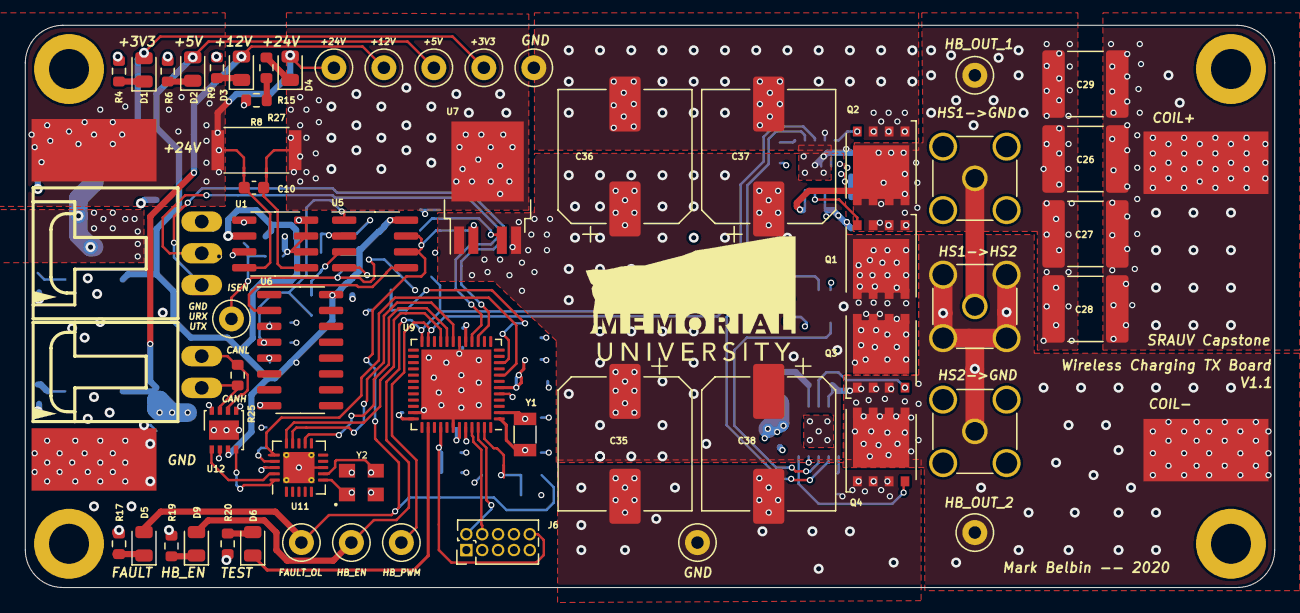
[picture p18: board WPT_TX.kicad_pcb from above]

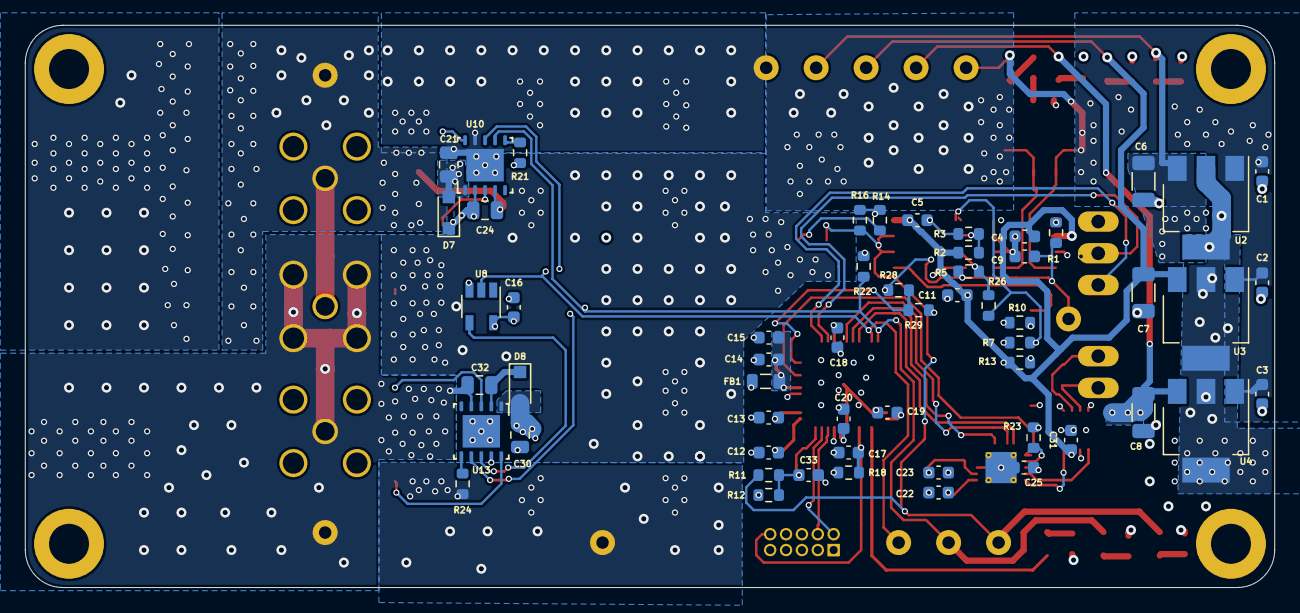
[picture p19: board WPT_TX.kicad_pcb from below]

Board: 4 copper layers, 100.0 x 45.0 mm, 124 parts (56 on the bottom side), 64 nets.

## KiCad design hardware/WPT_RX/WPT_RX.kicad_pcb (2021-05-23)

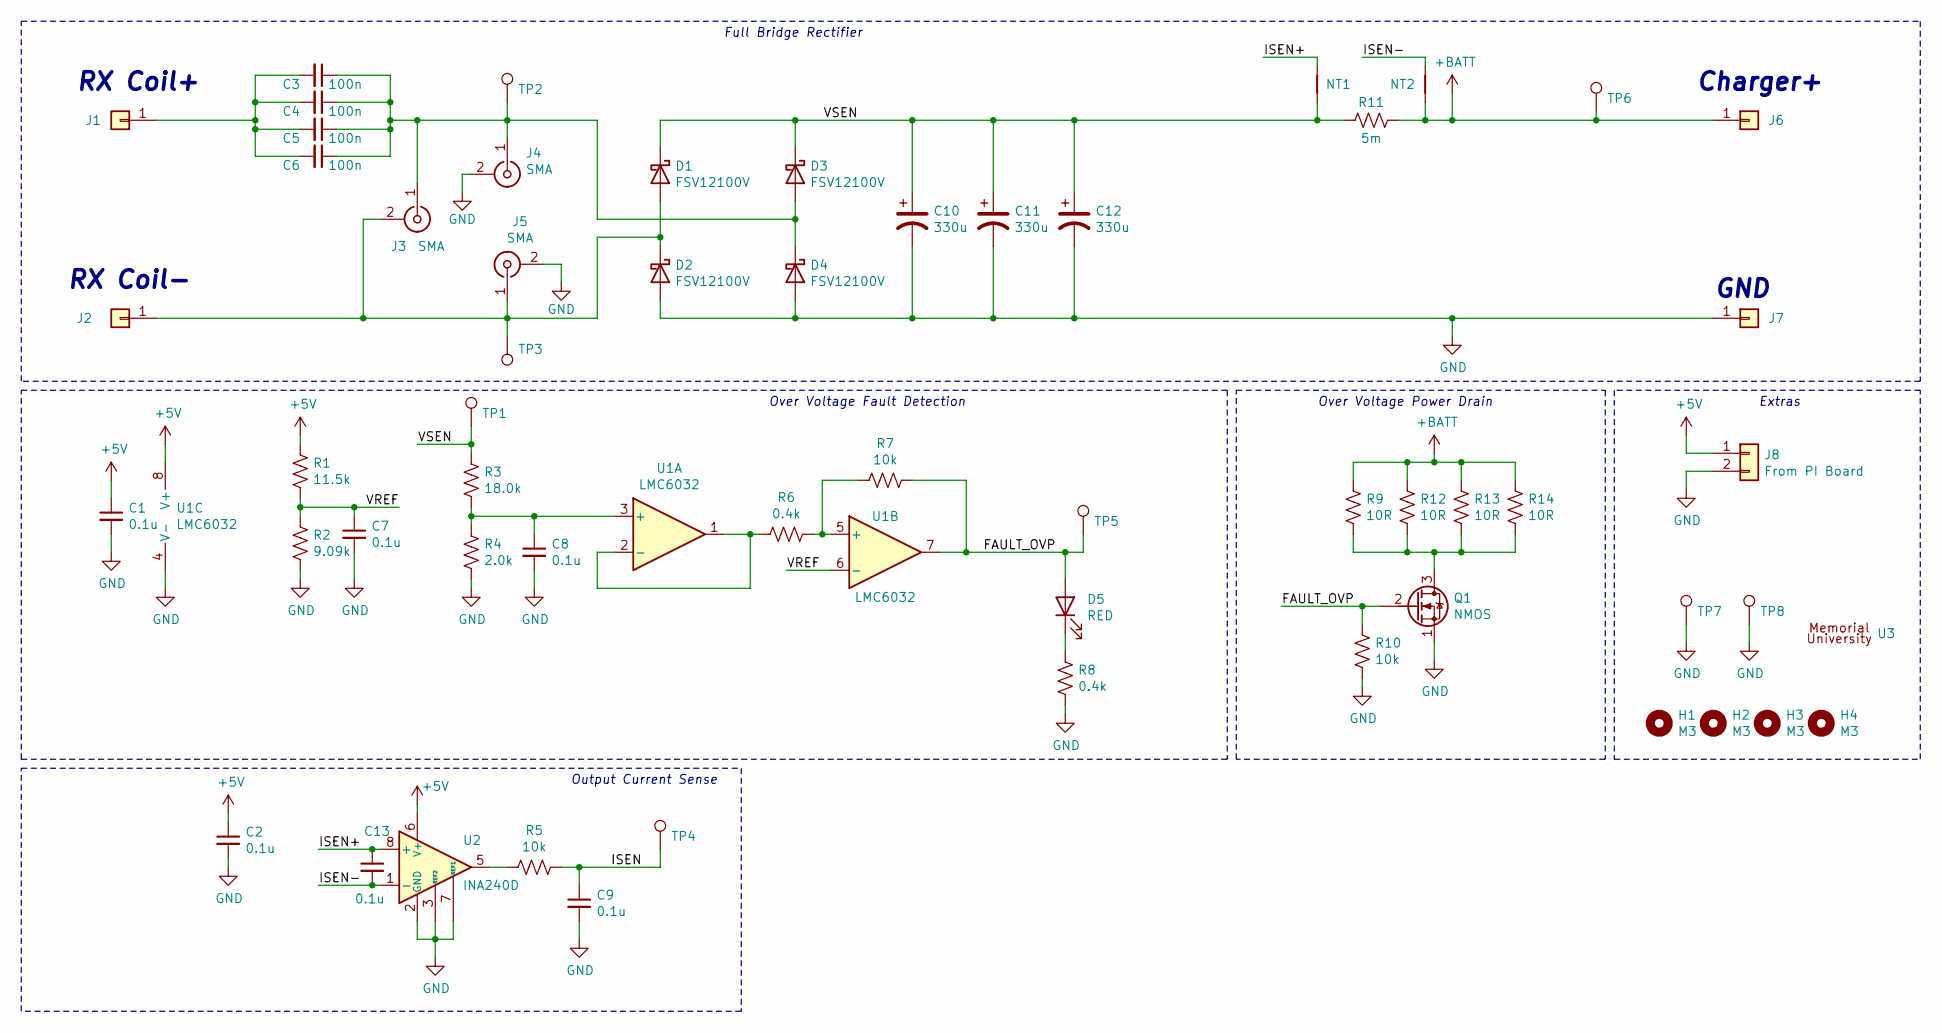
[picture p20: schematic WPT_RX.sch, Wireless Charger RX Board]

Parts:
C1, C2, C7, C8, C9, C13: 0.1u; C_0603_1608Metric; Digikey 1276-1258-1-ND
C3, C4, C5, C6: 100n; C_2220_5650Metric; Digikey 490-16696-1-ND
C10, C11, C12: 330u; CP_Elec_10x12.5; Digikey 493-13765-1-ND
D1, D2, D3, D4: FSV12100V; TO-277B; Digikey FSV12100VCT-ND
D5: RED; LED_0805_2012Metric; Digikey 475-1415-1-ND
H1, H2, H3, H4: M3; MountingHole_3.2mm_M3_DIN965_Pad
J1, J2, J6, J7: Conn_01x01; SolderWirePad_single_SMD_5x10mm
J3, J4, J5: SMA; SMA_Amphenol_901-144_Vertical; Digikey WM17068-ND
J8: From PI Board; 70553-02; Digikey WM4900-ND
NT1, NT2: Net-Tie_2; NetTie-2_SMD_Pad0.25mm
Q1: NMOS; TDSON-8-1; Digikey 448-IAUC70N08S5N074ATMA1CT-ND
R1: 11.5k; R_0603_1608Metric; Digikey RMCF0603FT11K5CT-ND
R2: 9.09k; R_0603_1608Metric; Digikey RMCF0603FT9K09CT-ND
R3: 18.0k; R_0603_1608Metric; Digikey P18KDBCT-ND
R4: 2.0k; R_0603_1608Metric; Digikey 541-2790-1-ND
R5, R7, R10: 10k; R_0603_1608Metric; Digikey RHM10KDCT-ND
R6, R8: 0.4k; R_0603_1608Metric; Digikey PAT400ACT-ND
R9, R12, R13, R14: 10R; TO-220F-2_Horizontal_TabDown; Digikey PWR221T-50-10R0F-ND
R11: 5m; R_2512_Sense; Digikey YAG6124CT-ND
TP1, TP2, TP3, TP4, TP5, TP6: TestPoint; TestPoint_Loop_D1.80mm_Drill1.0mm_Beaded; Digikey 36-5117-ND
TP7, TP8: TestPoint; TestPoint_Loop_D1.80mm_Drill1.0mm_Beaded; Digikey 36-5001-ND
U1: LMC6032; SOIC-8_3.9x4.9mm_P1.27mm
U2: INA240D; SOIC-8_3.9x4.9mm_P1.27mm; Digikey 296-48837-ND
U3: MUN; MUNLOGO

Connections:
+5V: C1.1, C2.1, J8.1, R1.1, U1.8 (V+), U2.6 (V+)
+BATT: J6.1, NT2.1, R9.1, R11.2, R12.1, R13.1, R14.1, TP6.1
/FAULT_OVP: D5.2 (A), Q1.2 (G), R7.1, R10.1, TP5.1, U1.7
/ISEN: C9.1, R5.2, TP4.1
/ISEN+: C13.1, NT1.1, U2.8 (+)
/ISEN-: C13.2, NT2.2, U2.1 (-)
/VREF: C7.1, R1.2, R2.1, U1.6 (-)
/VSEN: C10.1, C11.1, C12.1, D1.1 (K), D3.1 (K), NT1.2, R3.1, R11.1, TP1.1
GND: C1.2, C2.2, C7.2, C8.2, C9.2, C10.2, C11.2, C12.2, D2.2 (A), D4.2 (A), J4.2 (Ext), J5.2 (Ext), J7.1, J8.2, Q1.1 (S), R2.2, R4.2, R8.1, R10.2, TP7.1, TP8.1, U1.4 (V-), U2.2 (GND), U2.3 (REF2), U2.4 (GND), U2.7 (REF1)
unnamed: C3.1, C4.1, C5.1, C6.1, D3.2 (A), D4.1 (K), J3.1 (In), J4.1 (In), TP2.1
unnamed: C3.2, C4.2, C5.2, C6.2, J1.1
unnamed: C8.1, R3.2, R4.1, U1.3 (+)
unnamed: D1.2 (A), D2.1 (K), J2.1, J3.2 (Ext), J5.1 (In), TP3.1
unnamed: D5.1 (K), R8.2
unnamed: Q1.3 (D), R9.2, R12.2, R13.2, R14.2
unnamed: R5.1, U2.5
unnamed: R6.1, R7.2, U1.5 (+)
unnamed: R6.2, U1.1, U1.2 (-)

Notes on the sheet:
RX Coil+
RX Coil-
Charger+
GND
Output Current Sense
Over Voltage Fault Detection
Over Voltage Power Drain
Extras
Full Bridge Rectifier

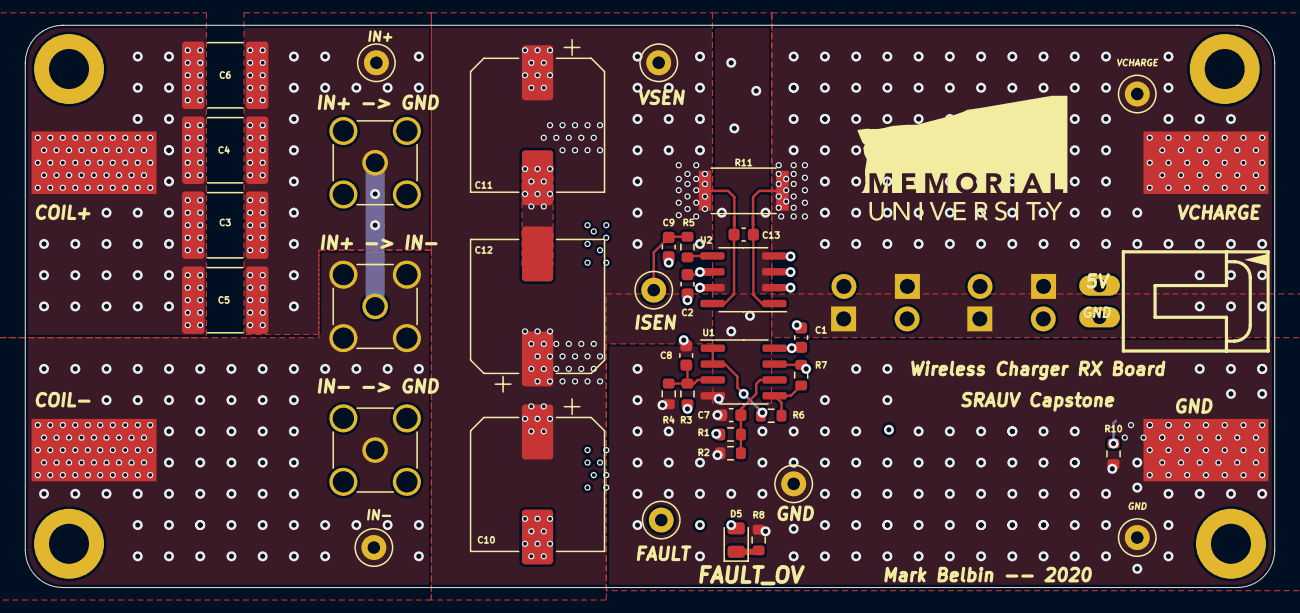
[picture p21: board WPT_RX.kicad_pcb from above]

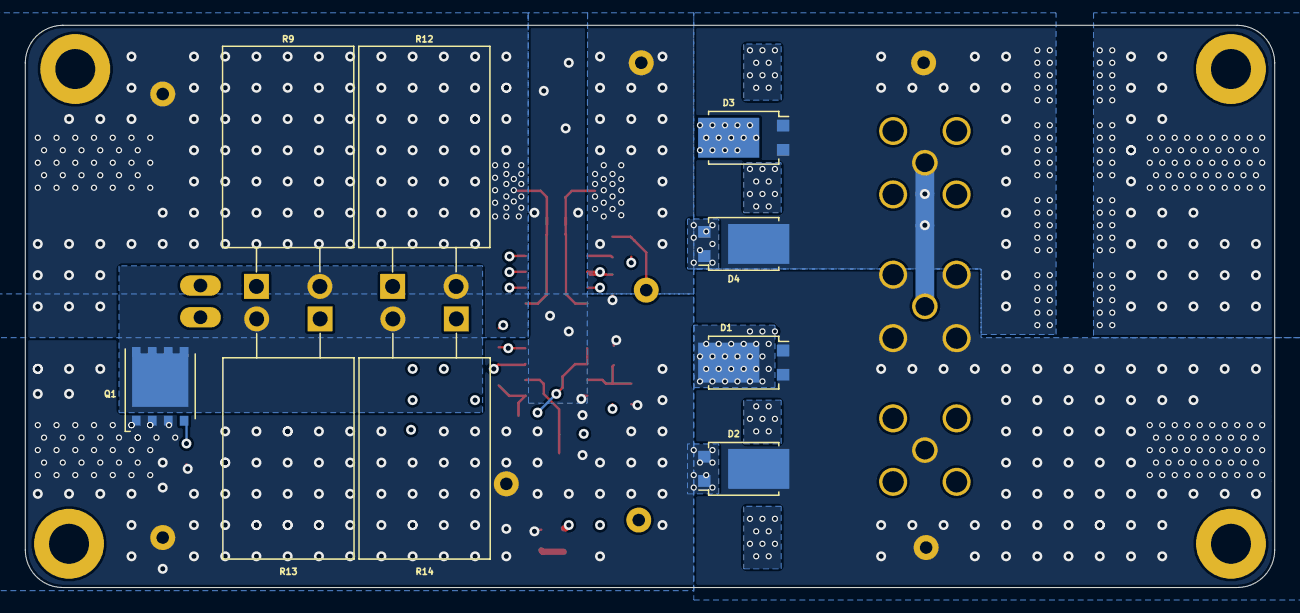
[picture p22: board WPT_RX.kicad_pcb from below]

Board: 4 copper layers, 100.0 x 45.0 mm, 58 parts (9 on the bottom side), 18 nets.

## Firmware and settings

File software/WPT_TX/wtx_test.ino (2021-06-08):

const int HBridge_PWM = 2; //Add pins here
const int HBridge_EN = 5;
const int ISEN = A4;

float current = 0;

void setup() {
  pinMode(HBridge_PWM, OUTPUT);
  pinMode(HBridge_EN, OUTPUT);
  
  delay(1000);  //Wait after powering on.

  /*//Optional Printing
  Serial.println("Starting WTX in 3");
  delay(1);  
  Serial.print("...2");
  delay(1);  
  Serial.print("...1");
  delay(1);  
  Serial.print("....POW");*/

  digitalWrite(HBridge_EN, HIGH);
  tone(HBridge_PWM, 100000); // 100kHz default
}

void loop() {
 //Do Nothing
}

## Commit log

2021-05-23 Added Original Files
    - Transferred over files from original senior design project repo.
    - Organized files into hardware, software, and simulation folders.
    [705430003.STEP, 705530001.STEP, 705530002.STEP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]
2021-05-23 Schematics
    - Add sch pdfs to additional folder in hardware for readability.
2021-05-23 More README Images
    - Added topology circuit images.
2021-05-23 Added circuit images
    - Topology circuit images
2021-05-23 Schematic images
    - Added snips of each board schematic
2021-05-23 More Images
    - Schematic images
2021-05-25 Schematic Updates
    - Removed "HD" net label from HB pins on gate drivers. This resulted in a critical failure on the original board and was fixed with a bodge.
    - Added an extra voltage divider to ISEN input to reduce chance of 5V overvolt scenario.
    - Increased series resistor value for blue LEDs by a factor of 2. Waaaay too bright.
    - Decreased series resistor for 3V3 LED indicator, too dim.
    [WPT_TX.sch]
2021-05-25 Updated PCB
    - Added four extra resistors from schematic changes to PCB.
    - Removed HD connections in gate driver layout.
    - Regenerated gerbers
    [WPT_TX-B_Cu.gbr, WPT_TX-B_Mask.gbr, WPT_TX-B_SilkS.gbr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]

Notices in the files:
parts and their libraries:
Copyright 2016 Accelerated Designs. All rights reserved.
